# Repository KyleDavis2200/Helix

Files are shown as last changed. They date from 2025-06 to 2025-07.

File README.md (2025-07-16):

# Helix
Helix is an antweight ring spinner combat robot that uses its large weapon to protect itself from its opponents, instead of using normal armor.


# Features

* 10" asymmetric AR500 steel weapon spinning at over 260 MPH with 128 joules of energy!
* Vertical element to the weapon's counterweight blocks attacks from horizontal spinners before they hit the robot itself.
* Dual RS2205 Brushless Weapon Motors
* Tangent drive with tank treads.
* Carbon fiber frame
* Durable TPU body with ultra lightweight design.
* Custom PCB that serves as a switch, series board for the batteries, and a BEC for the receiver.

# Images
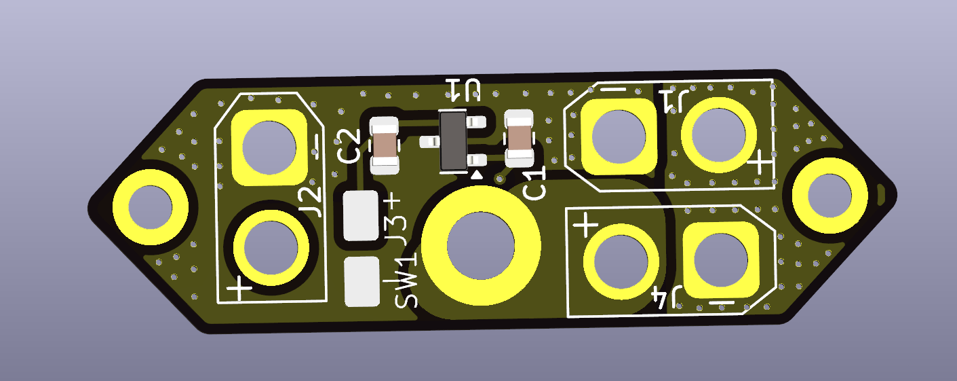
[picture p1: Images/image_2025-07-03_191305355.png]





# Background

Combat robotics has been one of my main hobbies ever since I joined my school's combat robotics team at the beginning fot he 2023-2024 school year. Throughout that time, I have mainly spent my time building 15lb eggbeater combat robots, where, due to the time and money invested into them, we are often scared to go too far outside of the box since a small design flaw could mean thousands of dollars and hundreds of hours were wasted. Highway is the perfect opportunity to make something outside of the box, as complex and creative projects are rewarded. 

# Bill of Materials

|Item |Individual Cost|Quantity |Total Cost (Includes shipping)|Notes |
|---|---|---|---|---|
|Drive Motor Screw |8.75 |1 (pack of 25)|8.75 |*Only 8 in the robot |
|Drive Standoff/WM Screw |6.4 |30 |6.4 |*Ordering extra screws in case some get lost or damaged. 24 are used in the robot. |
|Main Screw |4.36 |12 |4.36 |*Ordering extra screws in case some get lost or damaged. 8 are used in the robot. |
|M3 Plastite |5.69 |1(Pack of 25) |5.69 |*Only 6 in the robot |
|4in1 ESC |38.8 |1 |38.8 | |
|PCB |9.62 |1 |9.62 | |
|Battery |9.25 |2 |18.5 |*Need 2 because the robot uses 2 at once |
|Carbon Fiber Parts |29.1 |1 |29.1 | |
|Weapon |18.47 |2 |36.94 |*Only 1 is used in the robot, other is a spare |
|Bearing Washer |0.77 |5 |3.85 |*4 are used in the robot, 5th is a spare |
|Weapon Bearing |12.99 |1 (Pack of 10)|12.99 |*4 are used in the robot |
|Standoff |3.06 |1 (Pack of 5) |3.06 |*4 are used in the robot |
|Drive Standoff |8.99 |1 (Pack of 10)|8.99 |*8 are used in the robot |
|Repeat Tangent Drive Motor |22.5 |2 |45 |*2 are used in the robot |
|RS2205 Weapon Motor |7.6 |2 |15.2 |*2 are used in the robot |
|XR2 Receiver |9.99 |1 |9.99 | |
|Digikey |18.54 |1 |18.54 |*1x AP7381-50SA-7, 1x 2.2 uF 0805 Ceramic Cap, 1x 1 uF 0805 Ceramic Cap, 3x XT30 used on PCB, bought some extras because I'm new to soldering and am scared to mess it up|
| | | | | |
|8x M3 Washer |N/A |N/A |N/A |*Already Have |
|M5 x 12mm Screw |N/A |N/A |N/A |*Already Have |
|2x M5 Nut |N/A |N/A |N/A |*Already Have |
|M5 Washer |N/A |N/A |N/A |*Already Have |
|M3 Screw for Switch |N/A |N/A |N/A |*Already Have |
|M3 Nut for Switch |N/A |N/A |N/A |*Already Have |
|2x M2 Screws for PCB Mounting|N/A |N/A |N/A |*Already Have |
|2x M2 Screws for PCB Mounting|N/A |N/A |N/A |*Already Have |
|PLA Filament |N/A |N/A |N/A |*Already Have |
|TPU Filament |N/A |N/A |N/A |*Already Have |
|Nylon Filament |N/A |N/A |N/A |*Already Have |
| | | | | |
|Battery Charger |N/A |N/A |N/A |*Planning to buy myself |
|Transmitter |N/A |N/A |N/A |*Planning to buy myself because I want something a little nicer than what would be fair to buy from Hack Club's money |
| | | | | |
|Testing Cage |N/A |N/A |N/A |*Have access to one through my school's combat robotics team |
| | | | | |
| | | | | |
|Total |N/A |N/A |275.78 | |

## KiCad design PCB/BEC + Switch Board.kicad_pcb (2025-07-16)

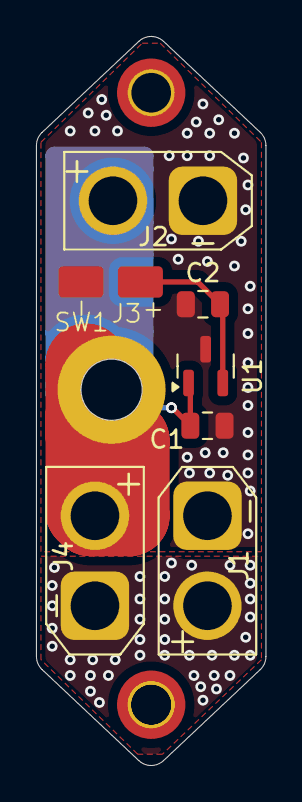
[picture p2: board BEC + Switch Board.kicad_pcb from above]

Board: 2 copper layers, 12.8 x 40.5 mm, 8 parts (1 on the bottom side), 4 nets.

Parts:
C1: 1uF; C_0805_2012Metric
C2: 2.2uF; C_0805_2012Metric
J1, J2, J4: Conn_01x02_Socket; AMASS_XT30U-M_1x02_P5.0mm_Vertical
J3: Conn_01x02_Socket; SignalWirePads
SW1: SW_DIP_x01; Screw Switch
U1: AP7381-50SA-7; SOT-23

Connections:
/GND: C1.1, C2.1, J1.2, J2.2, J3.2, U1.3 (GND)
unnamed: J1.1, J4.2
unnamed: C1.2, J2.1, U1.1 (VI)
unnamed: C2.2, J3.1, U1.2 (VO)

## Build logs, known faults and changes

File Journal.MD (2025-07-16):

---
title: Helix
author: Kyle Davis
description: A ring spinner antweight combat robot with a custom PCB for power distribution.
created_at: 2025-06-13
---

Total Time 28.75 Hours

6/13/2025

4 Hours

I began this project by searching for excuses to make an overly complicated combat robot. Combat robotics is my main hobby, but I have never ventured far outside of the meta out of fear of wasting time and money on an unsucessful bot. Hack Club's Highway program rewards projects that are extra complex with a higher budget and more points in the program. I saw this as the perfect opportunity to make a more complicated robot design. My previous experience in combat robotics comes from my 15lb robot, Dino, which I have placed 2nd and 3rd with at NRL Nationals over the last 2 years. Dino uses an eggbeater style weapon, which is very common and relatively simple. For this project I am going to use a more complicated weapon system, and maybe even a custom PCB, to make my project more complicated to warrant the higher budget and more points in Highway. This is something I have always wanted to do as well, as these more mechanically complex robots are always very fascinating, but Highway gave me the perfect justification to pull the trigger on it.

My first idea was to make a hammersaw, which uses a spinning weapon on an arm to attack the tops of other robots. However, the hammersaw has been very popular over the last year or two, especially in insectweights. This has led to the systems/parts needed to run a hammersaw being relatively well documented. I opted not to build a hammersaw as the well documented and convergant nature of hammersaw electronics/mechanics may cause me to not get the full points for Highway, which I would need to fund the build.

This led me to think about the most complicated robot designs I could think of, to make sure I could earn the full points and budget from Highway. My mind instantly went to ring spinners, which are typically very complicated due to the difficulty of constraining and powering such a thin blade. The advantage of this, however, is that you can build a robot where the blade sticks far enough out from your robot where you are able to reach your opponent while they have nowhere to target on your robot. I've always loved the idea of having a ring spinner, but I never quite fell in love with the idea of designing one, mostly due to the mechanical complexity. However, since I need complexity for this project, this is perfect as I am more comfortable adding mechanical complexity than electrical complexity.

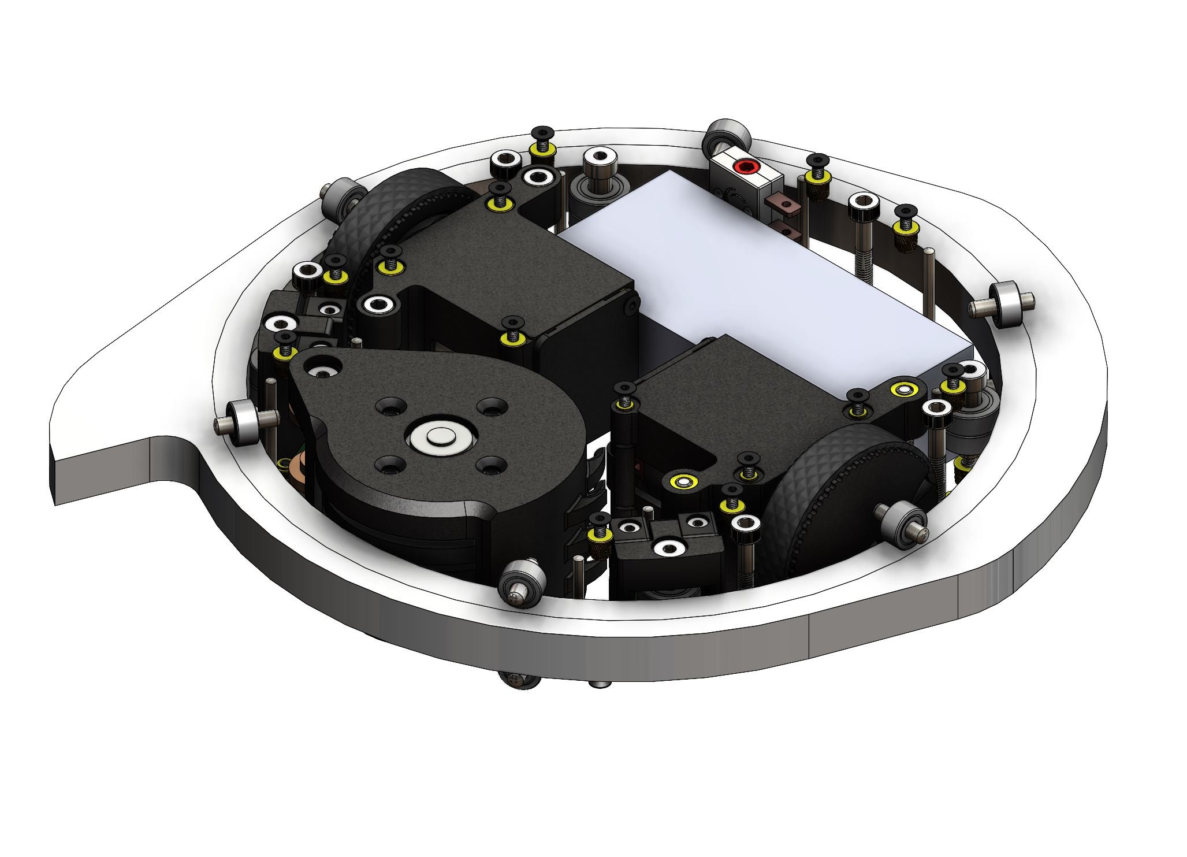
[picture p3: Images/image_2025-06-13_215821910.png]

An example of a ring spinner robot.

The first thing I did was design a rough blade concept. Some aspects of this design, such as the blade thickness, were based off of other antweight robots, such as the scalar kit. The amount of support everywhere around the blade was approximated by eyeballing it. I may attempt to use FEA in the future, but generally eyeballing works well enough in combat robotics(its also very difficult to approximate combat robotics collisions with FEA), especially after being in the community long enough to "calibrate" your eyeballing. This concept allowed me to check the mass of the blade, which I could then use to make sure that it would be possible to fit the robot in the weight limit. At 159 grams, the blade was very heavy, but its reach meant that I could get away with budgeting less weight for armor, giving me confidence that it would be possible to fit it within the weight limit.

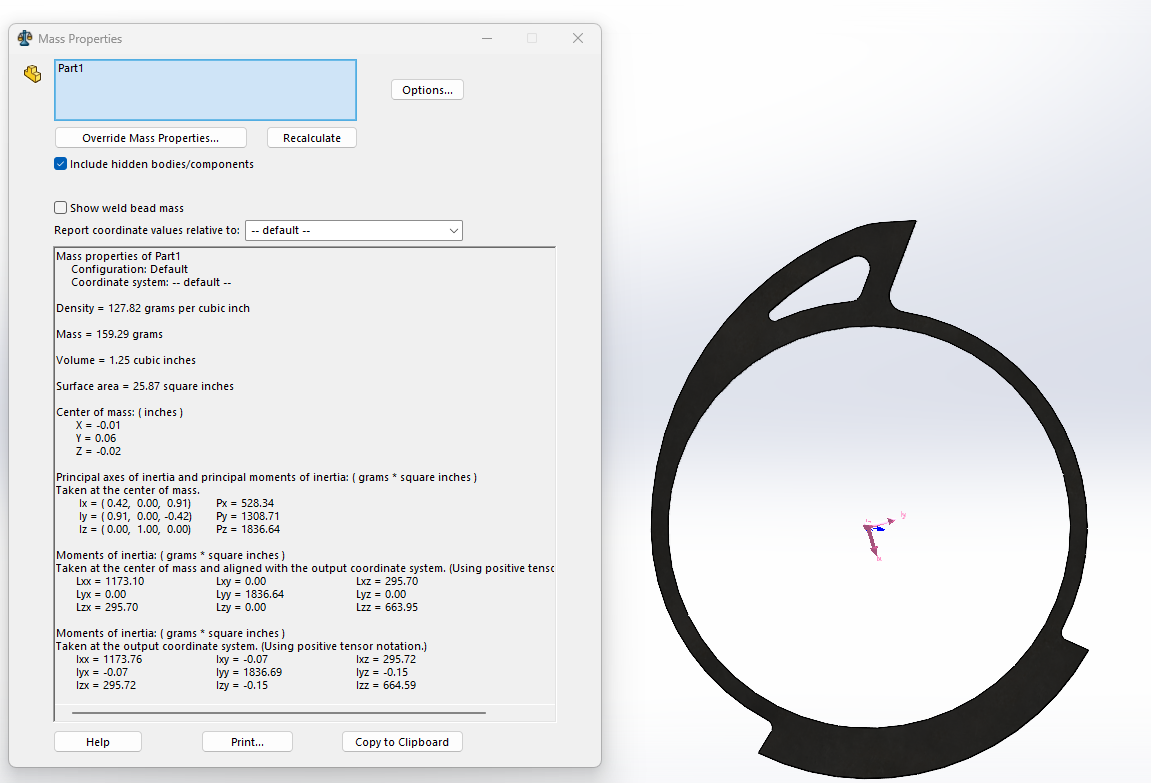
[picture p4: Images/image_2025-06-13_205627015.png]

The first blade design.

This design also allowed me to get a rough interior diameter of six inches, which I can then use to begin laying out the rest of the robot's design. Ideally, I would decrease this diameter, but I first had to make sure I could fit my electronics in it. The next step is to find the bearings I am going to use. This will allow me to get an idea of how much space I have for the electronics, as everything else can move more freely than the bearings. My initial plan was to have bearings above and below the blade, which would have constrained it axially. I did not consider that this would provide no radial constrainment, leading to the need for even more bearings. This system would have needed at least 9 bearings, and at 4g per bearing this would not be optimal with already being tight on weight from the large weapon. Instead, I am going to opt to use flanged ball bearings, where I can get away with using only 6 or less bearings at a relatively similar weight to the ball bearings above. This approach has its own flaw however. The flange on the bearings is so small that it may not provide enough axial constrainment by itself. To supplement them, I am going to use washers between the flange and the weapon ring. Since the washer goes all the way around the bearing, it has much more surface area constraining it, and the higher diameter of the washer allows it to provide more surface area for the weapon. At this point I realized I am likely going to greatly exceed the speed ratings on these bearings, which is normal for combat robots as they are only used for very short periods of time, however not to this extent as I may exceed 100k rpm on these bearings. There's not really anything I can do about that though so it is what it is.

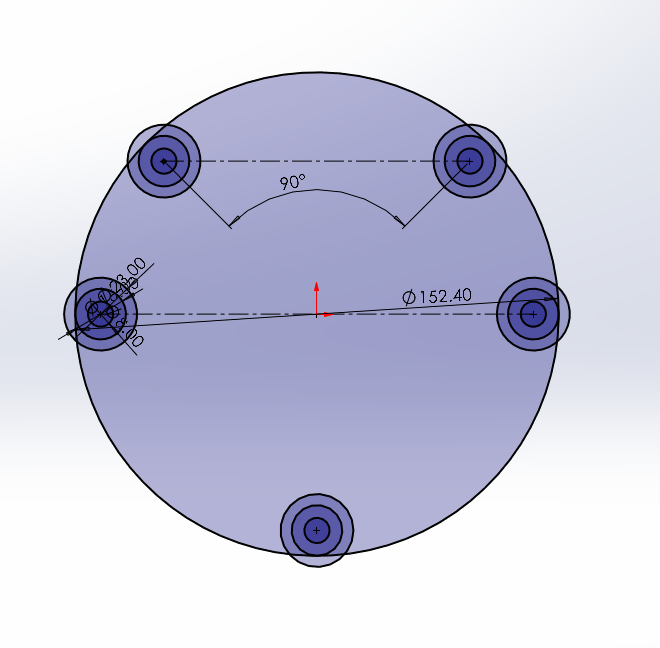
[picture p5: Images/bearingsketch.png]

Current sketch of the internals of the robot.

The next step was to choose my drive system. To keep everything on the robot simple I am going to use a tangent drive system. This eliminates the need for gearboxes or gear reduction as the motor output shaft uses friction to drive the wheels. Repeat Robotics sells motors designed specifically for this usage in this weight class, so I will use those. I plan on coupling this with Lego wheels, as that seems to be a very standard pairing. However, if the diameter of these wheels ends up being significantly larger than the height of the rest of the robot, I may opt for smaller custom wheels instead. At this point I also modeled in a 4S 300mah LiPo battery and a Repeat 2822 weapon motor that would friction drive the ring through a TPU interface.

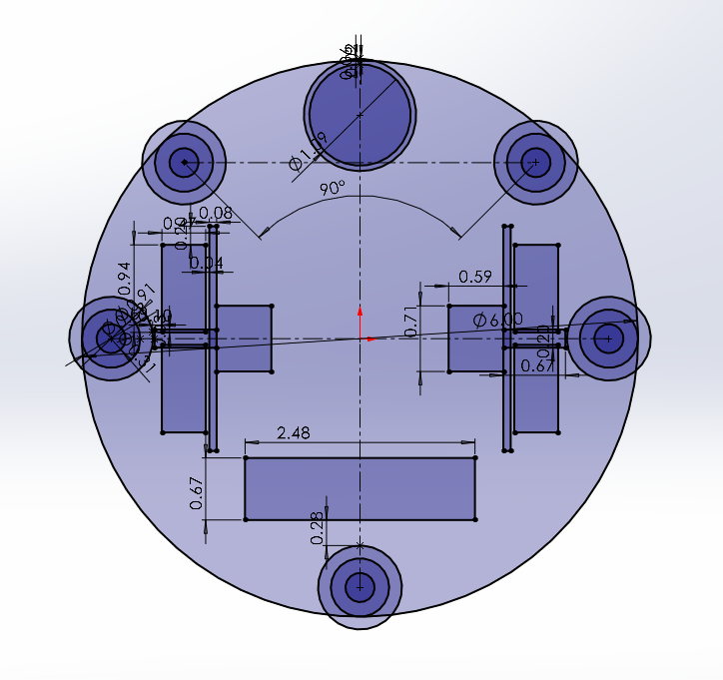
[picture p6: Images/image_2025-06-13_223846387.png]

Current design progress.

Clearly, I had way too much room on the inside at this point, so I chose to shrink it until I knew I could just barely squeeze the wiring in. This was important as the weight was approaching 324 grams, leaving approximately 120 grams left for the entire frame, receiver, wheels, receiver, and ESCs, but by shrinking the space I gave myself on the inside, I can shrink the weapon too, saving more weight.


Current weight.

By shrinking the internal ring diameter down to 5.25", I was able to knock a significant amount of weight out of the weapon, and this would also reduce the amount of weight spent in the remainder of the frame as the frame too would now be smaller. 

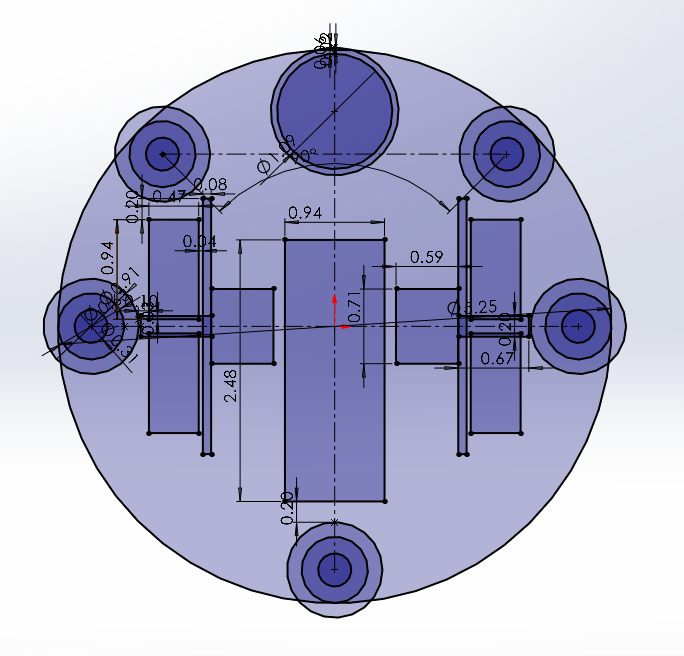
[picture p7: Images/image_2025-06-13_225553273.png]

Current internal layout.

I plan to proceed with this layout tomorrow as I model the frame, however I expect to encounter weight issues very shortly into my design process. My plan to save weight from there is to remove the rear bearing and reposition the remaining four bearings in a more square shape, allowing the battery to move further back and get rotated to fill up the created space. This would then allow me to shrink the robot more. This would save plenty of weight between the reduction in frame size, weapon size, and bearing count. I initially wanted to have five bearings as it would allow me to have three bearings supporting against the axial forces of upwards impacts and two against the axial forces of downwards(or, more likely, upwards impacts while inverted) impacts, however two of each would likely be plenty.

6/14/2025

6 Hours

Well, after thinking about it some more, I realized I should just got to the four bearing setup. This would save some weight and allow me to compact the robot more, which is always ideal. I would like to use extra weight for armor or for a fork on the back of the robot(unconventional for a ring spinner but counters the counter to the weapon). I also realized that the Repeat 2822 weapon motor that I planned on using would have been too big, sticking out past the top plate, and would have caused the robot to not be invertible. Instead, I replaced it with two 2205 drone motors, which should provide more than enough power. A single one of these motors could probably spin up the weapon, just barely, but due to the size of the weapon more motor is ideal. 

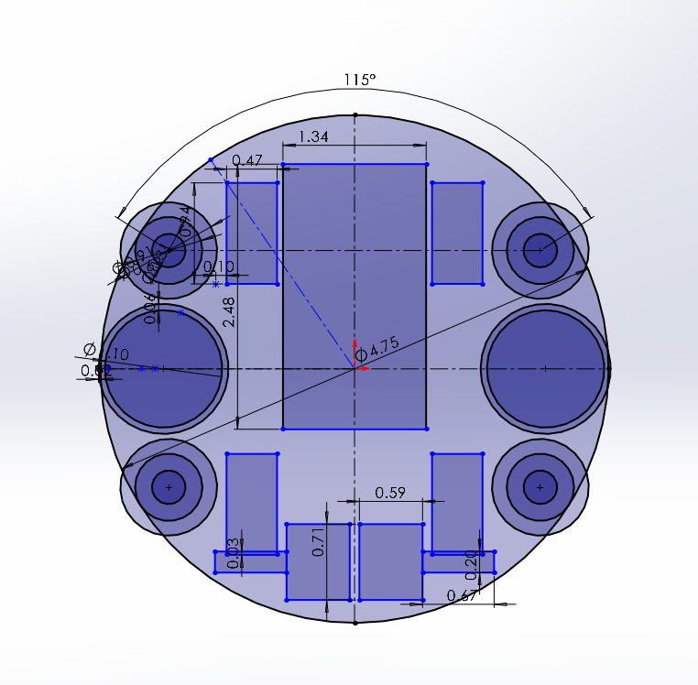
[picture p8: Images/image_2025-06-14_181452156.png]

This was the setup that I arrived at.

I still felt like there was a bit more space to be squeezed out. One of the flaws with this setup is I needed to find space for belts to power the front wheels, and I didn't leave much space for this. My next step was to look into using tracks instead of wheels, as these would allow me to save more internal space as I can use two small pulleys for each the front and back of the tracks, creating a more rectangular profile, saving space on the inside of the robot. I initially looked into silicone timing belts and silicone coated timing belts, but I would have need to custom order them. Next, I looked into using silicone wrist bands, but they would have been slightly too short. Instead, I opted to use round belts which I could make to the exact length that I needed by melting them together at the right length.

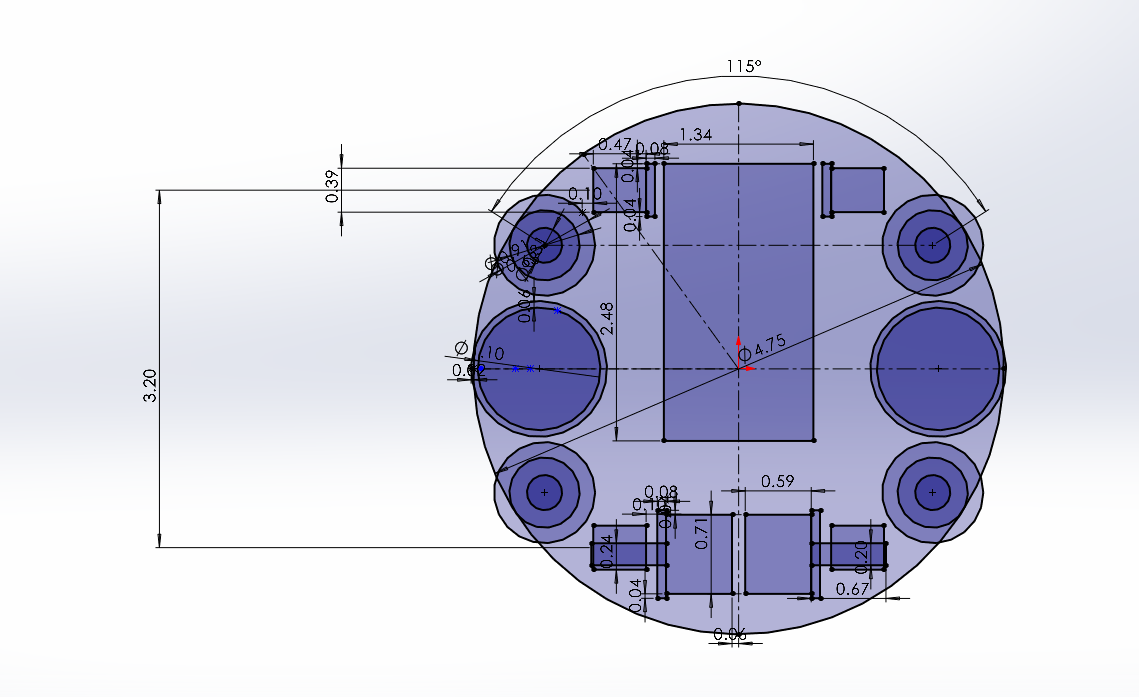
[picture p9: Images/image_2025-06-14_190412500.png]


This layout, with the space gained from the treads, was much more comfortable. Each track/belt weighed approximately 2 grams, which seemed bearable. Next, I made a sketch of the side of the robot, which would guide my extrusion thicknesses in the next step.

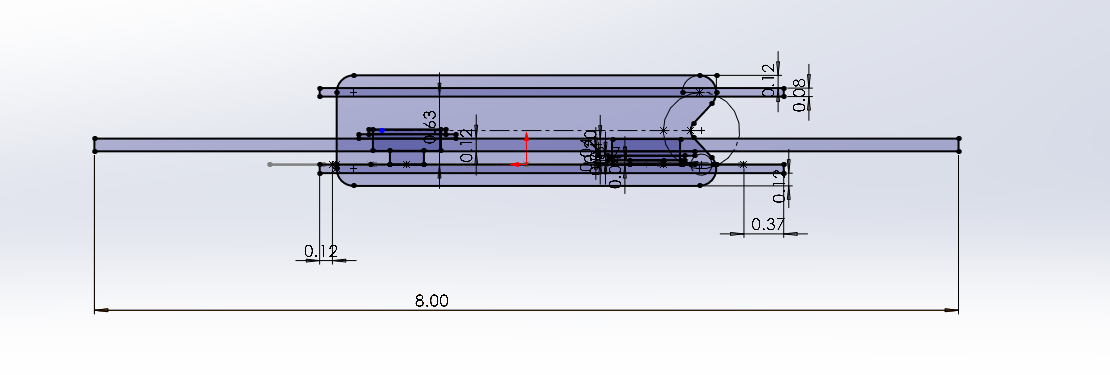
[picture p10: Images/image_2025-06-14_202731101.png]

Oops! All weapon (: !

Next, I extruded everything according to the sketches I made above. This outlines the construction of most of the robot's structure and its weapon system structure pretty well. The top and bottom of the robot are made of 2mm carbon fiber and provide most of the strength. There are 8mm aluminum standoffs in the four corners to hold the weapon bearings. Underneath and above each bearing are PLA spacers to get them at the right height. The bearings have aluminum washers on them to increase the surface area of the flanges in contact with the weapon, aiding in the axial constrainment. Two of the bearings have their flanges and washers under the weapon, and two of them have them above the weapon, to provide support in both directions. The next step is to implement the mounting for the drive pulleys and motors.

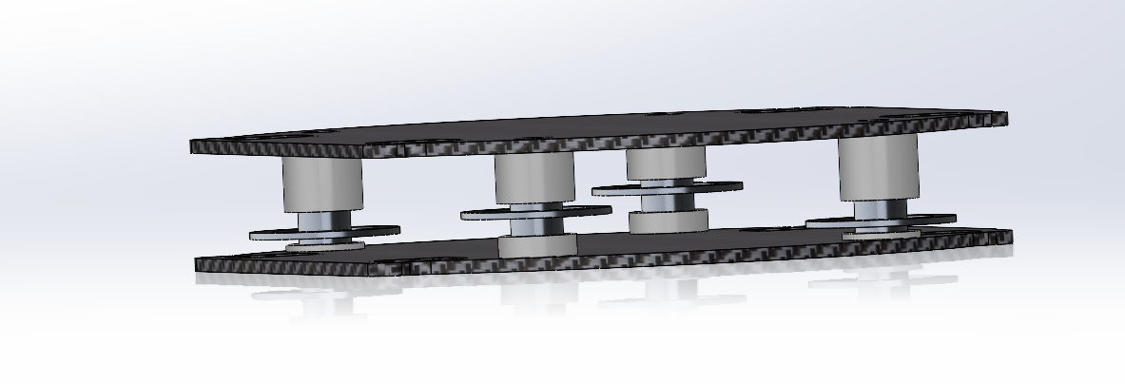
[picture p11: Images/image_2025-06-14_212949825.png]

Current design.

Instead of doing the productive next step I described above, I created an assembly file(I do my frame as a multibody part) and inserted the weapon.

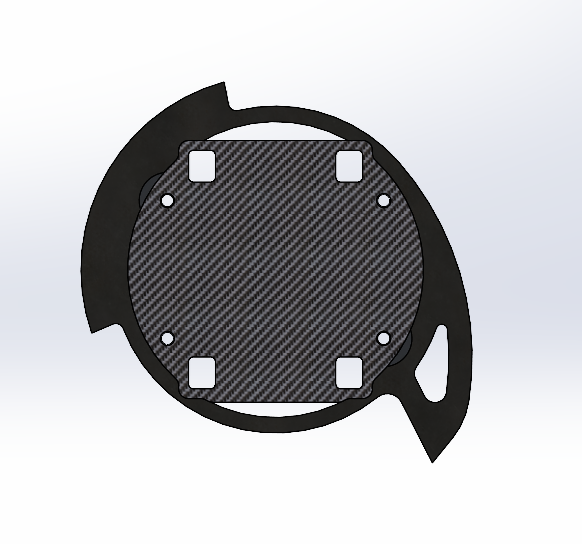
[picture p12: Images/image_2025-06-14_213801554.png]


Yeah this thing is ridiculous.

At this point I realized that the robot would be impossible to assemble due to the drive tracks needing to go through the top and bottom plates. I changed this by making cutouts in the top and bottom plate where they could be slid in between the treads. This also saved weight and removed a fragile area that was likely to result in the plates cracking. At this point I also realized I had to create cutouts in the top plate around the weapon (not pictured) motor since there was still 0.7mm of interference even after switching to a smaller motor. I may find a way to undo this or create a cover for it later, but for right now this is what I had to do.

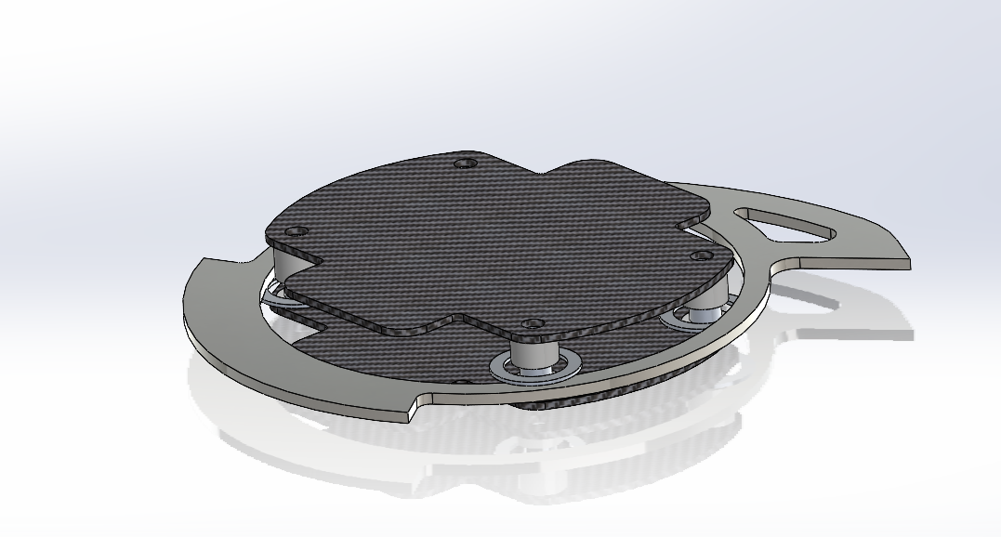
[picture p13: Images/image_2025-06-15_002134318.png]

Current design progress.

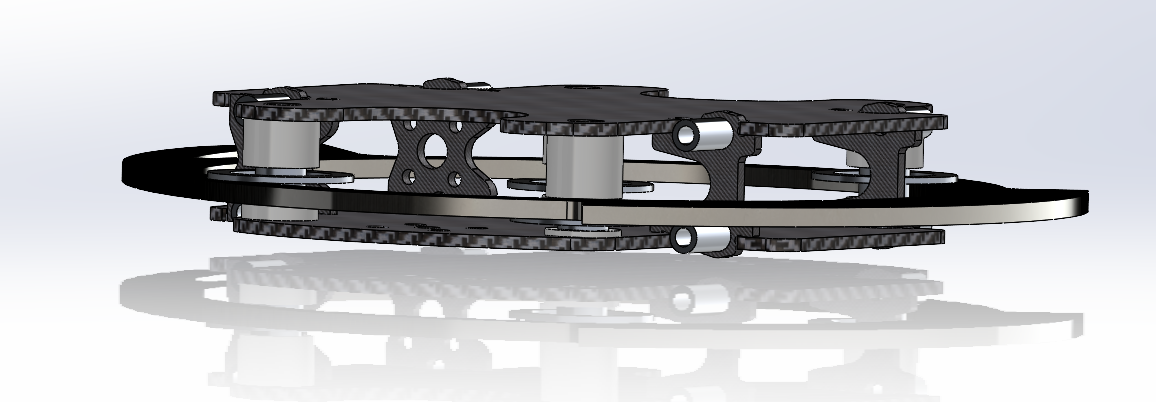
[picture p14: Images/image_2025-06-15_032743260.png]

At this point, I added all the features for mounting the drive motors and the drive pulleys. The mounting plates use dogbones to key into the top and bottom plates, allowing them to have a healthy amount of strength without using any fasteners yet. I will likely add a single screw to each plate later once I am adding the TPU armor.

At this point, I have about 100 grams left for ESCs, a series board for the batteries, a receiver, and any armor. Since each of those items besides the armor is just a couple grams I am not too worried about weight, but the armor weight can add up quickly. However, the whole idea behind this design was to "hide" behind the large weapon, so I am probably going to use very minimal armor.

6/15/2025

3 Hours

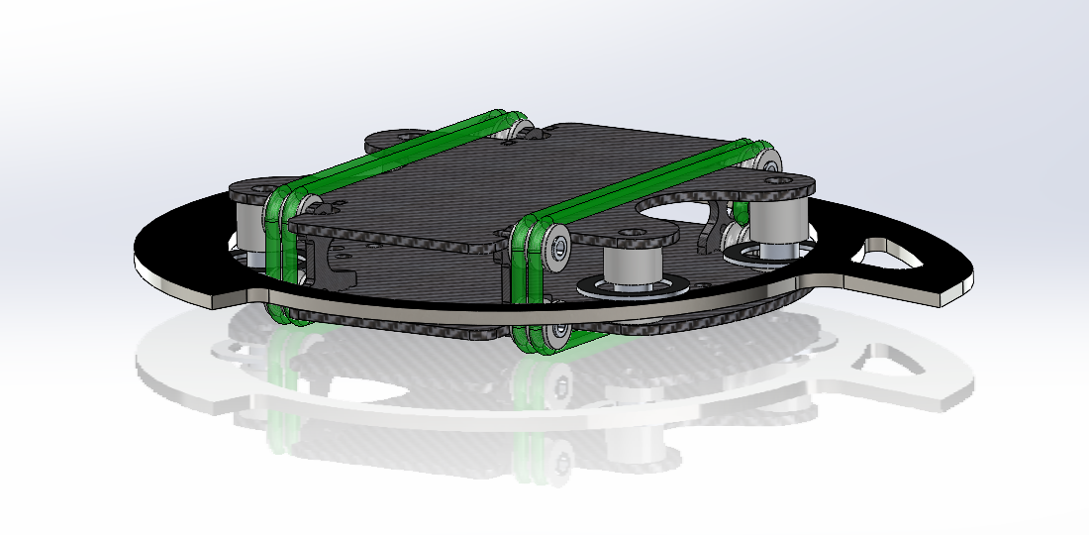
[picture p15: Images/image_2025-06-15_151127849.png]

At this point, I modeled in the drive pulleys and the belts/tracks. 

Now, I decided to add in the rest of the components into the model so that when I design the armor/body I know what I have to protect.
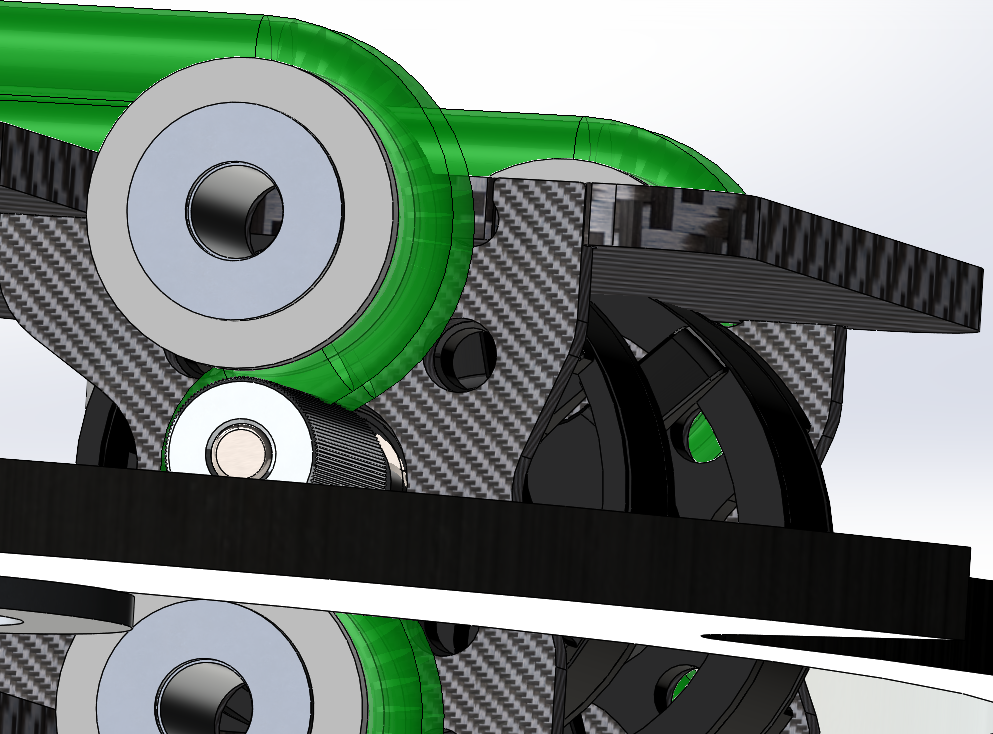
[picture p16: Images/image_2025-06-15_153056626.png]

Adding in the drive motors revealed a couple flaws. I messed up when calculating the interference for the drive belts, so the motors need to get moved to the back more or the pulleys need to move forwards (with the belts being made shorter accordingly). I also forgot to add the pockets for motor clearance in the top and bottom plates.

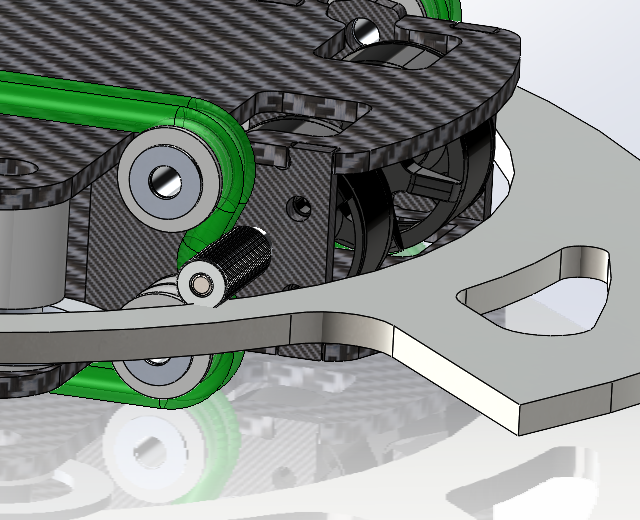
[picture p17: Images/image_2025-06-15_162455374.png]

At this point, I got the drive motors to pretty much fit, but I will need to trim the shafts. The other issue is that two of the motor mounting screws interfere with the wheel pulleys and standoffs, so I may need to use countersunk screws in carbon fiber, which is suboptimal but I don't have many other choices.

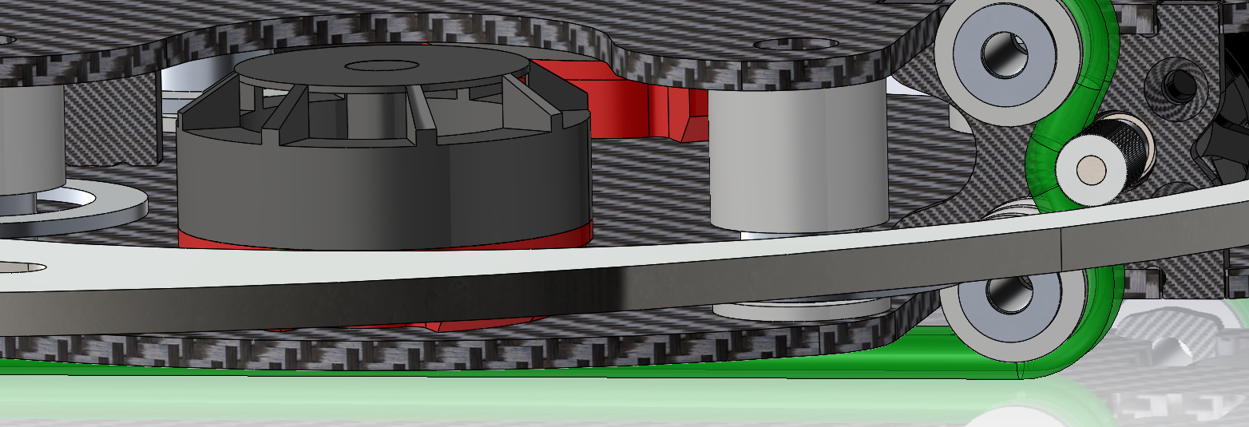
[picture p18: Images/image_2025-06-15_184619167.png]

Now, I countersunk the drive motor mounting screws, inserted the weapon motors, and cut down the shafts on both the drive motors and the weapon motors. The issue I am facing now is that the weapon motor has a red part where it mounts which does not spin, and that happens to line up perfectly at the height of the blade. Making my blade as low as possible is ideal against vertical spinners, so I wanted to keep the blade low, and mounting the motors to the top would make assembly more difficult, so instead I will solve this by thickening up the plastic(nylon or TPU, not sure yet) interface layer between the motor and the ring to be stiff enough where it can drive the ring without being directly supported by the motor can.

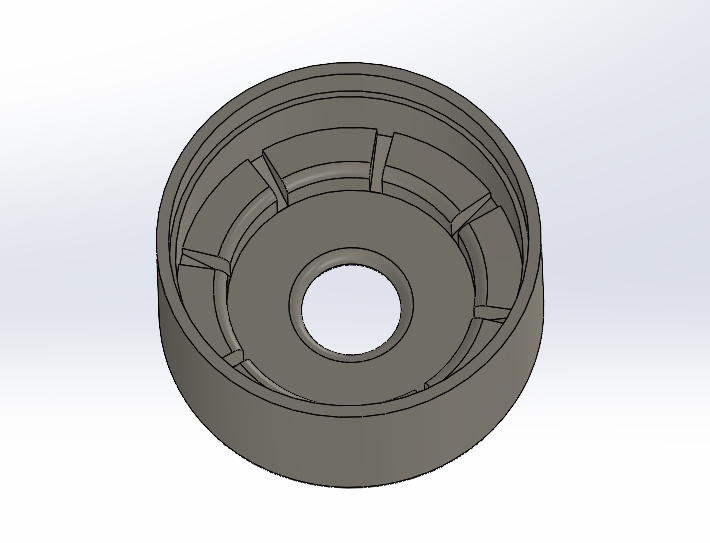
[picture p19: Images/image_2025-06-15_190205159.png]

The interface layer is a pretty simple part. Its basically just a cylinder with a keying feature for the top of the motor and a slight step to provide clearance for the part of the motor that does not spin. I will probably be gluing or taping this onto the motor as there is not a way to screw anything onto this motor with the shaft cut off and axial forces are not a concern.

6/25/2025

0.25 Hours

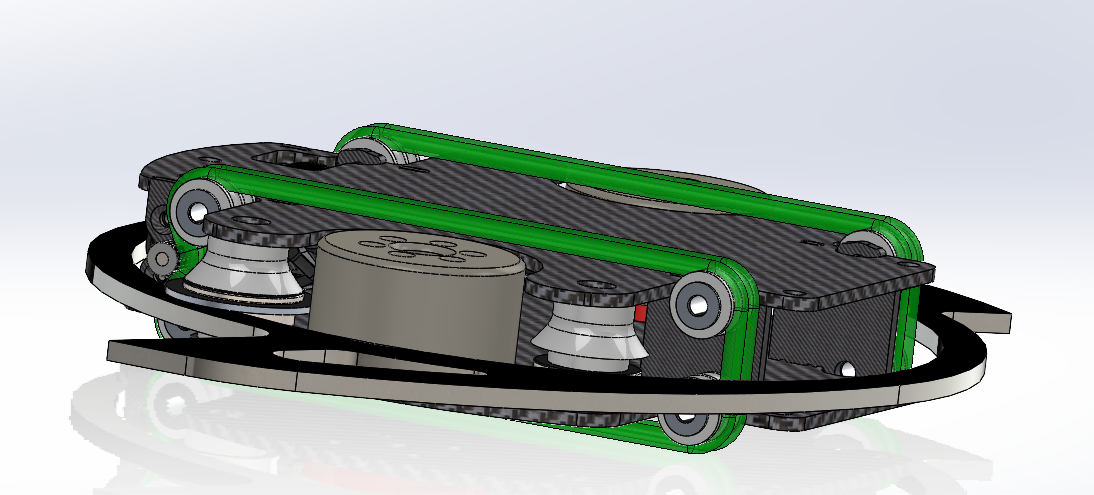
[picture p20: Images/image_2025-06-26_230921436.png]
 
Just barely worked on it today. Flared out a portion near the bottom of the upper spacers on each standoff to provide vertical support for the TPU body that will rest on it.

6/26/2025

4 Hours

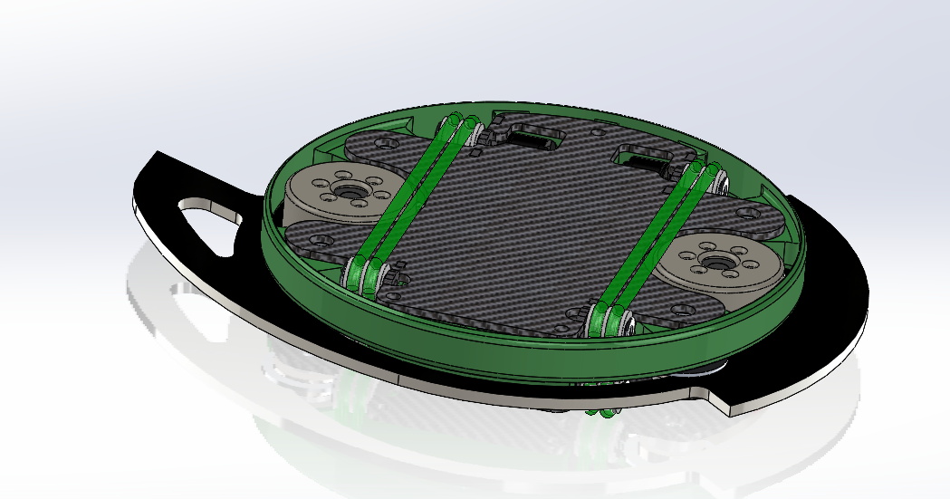
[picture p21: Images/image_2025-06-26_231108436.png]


Today I modeled a super minimal TPU body/armor for the robot that protects from attacks and serves to keep the electronics in. Since the whole concept of this robot revolves (haha) around the weapon serving as the first line of defense, this armor system was super minimal, generally consisting of 2-4 walls 0.4mm thick walls with low infil. Even if the weapon goes down, it still has a steel ring around the entire robot that will serve as armor. The TPU armor ring is generally spaced out from most of the robot's critical components, so if an opponent manages to hit it and tear through it, they'll be unable to hit anything that would cause significant damage.

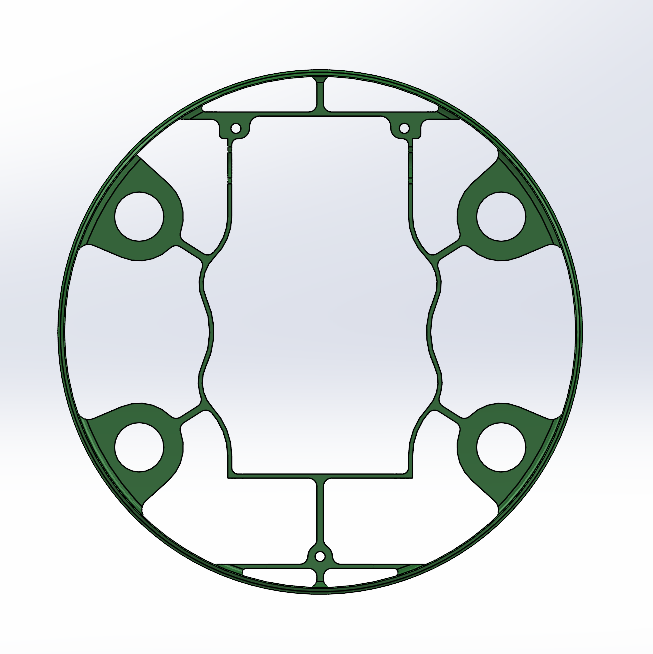
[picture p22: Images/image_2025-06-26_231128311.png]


On the inside of the robot, the armor has another layer that holds all of the electronics within the frame. This keeps everything in place and prevents wires from getting tangled in the motors.

7/1/2025

2 Hours

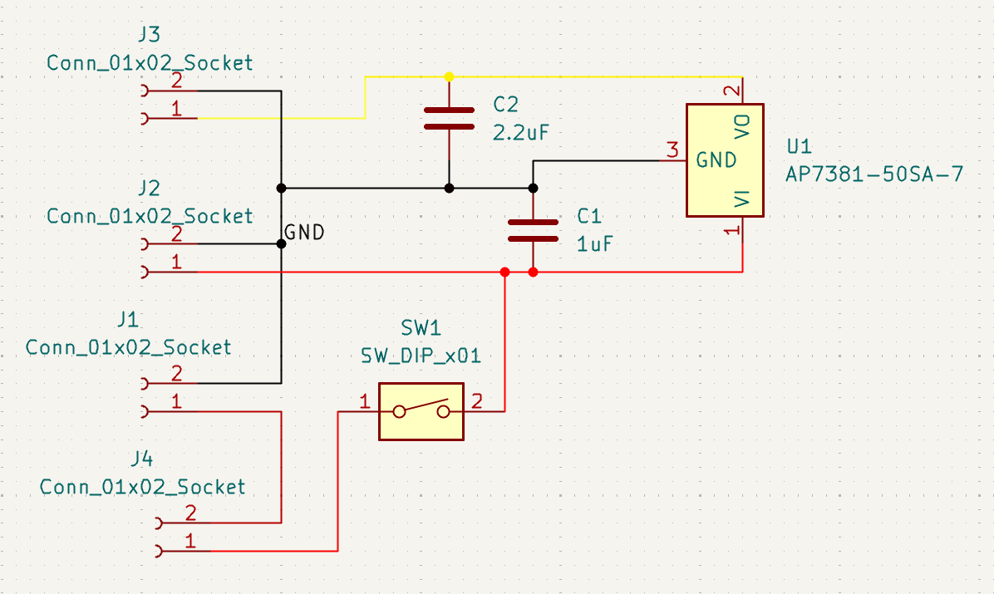
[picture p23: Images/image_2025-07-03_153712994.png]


Created a schematic for a basic PD Board / Switch / BEC for the robot. This was inspired by the Just Cuz Robotics PD Boards.

7/2/2025

4 Hours

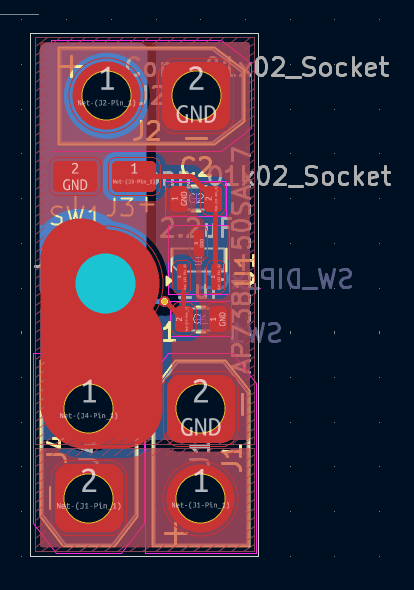
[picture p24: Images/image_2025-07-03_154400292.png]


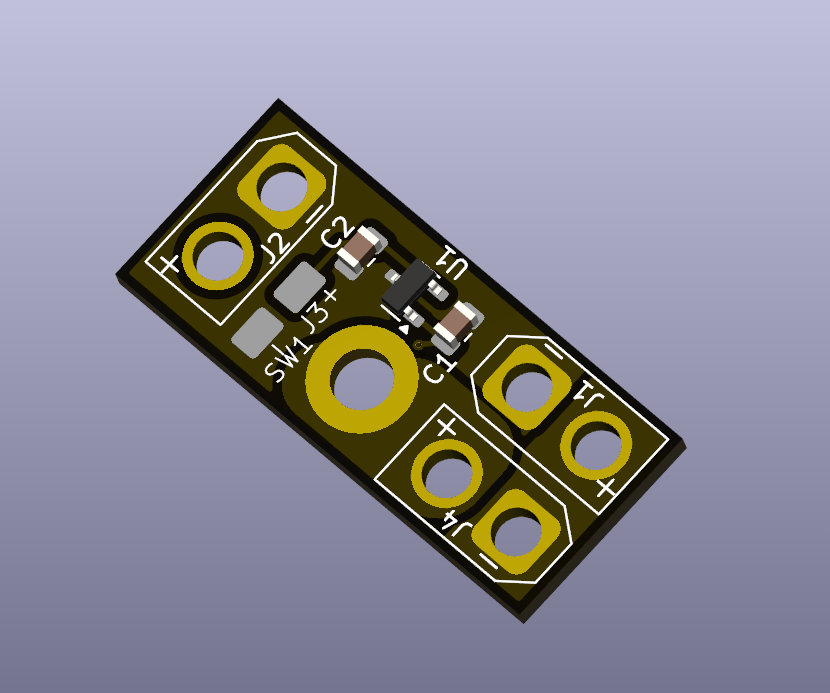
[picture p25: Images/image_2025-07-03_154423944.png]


Created a layout for the PCB. The board has two XT30 connectors to connect to each battery (batteries are in series), and a third to output power to the rest of the 4in1 ESC. The switch is an M3 screw with a nut soldered onto the board. There is a linear regulator that serves to create a 5V output for powering the receiver.

7/3/2025

3 Hours

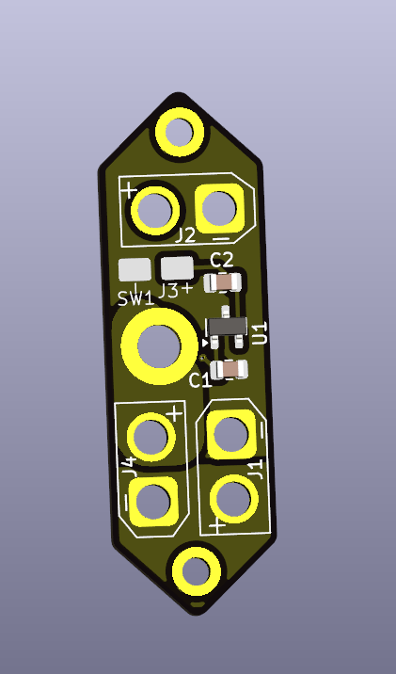
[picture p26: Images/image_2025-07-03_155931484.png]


Created mounting holes for the PCB. This will allow me to lock it in one place so the switch is always accessible, which is important for safety reasons. Last thing I have to do for this PCB is via stitching.



With via stitching done, the PCB is finalized and I can work on making a finalized BOM after I get a quote from JLCPCB.

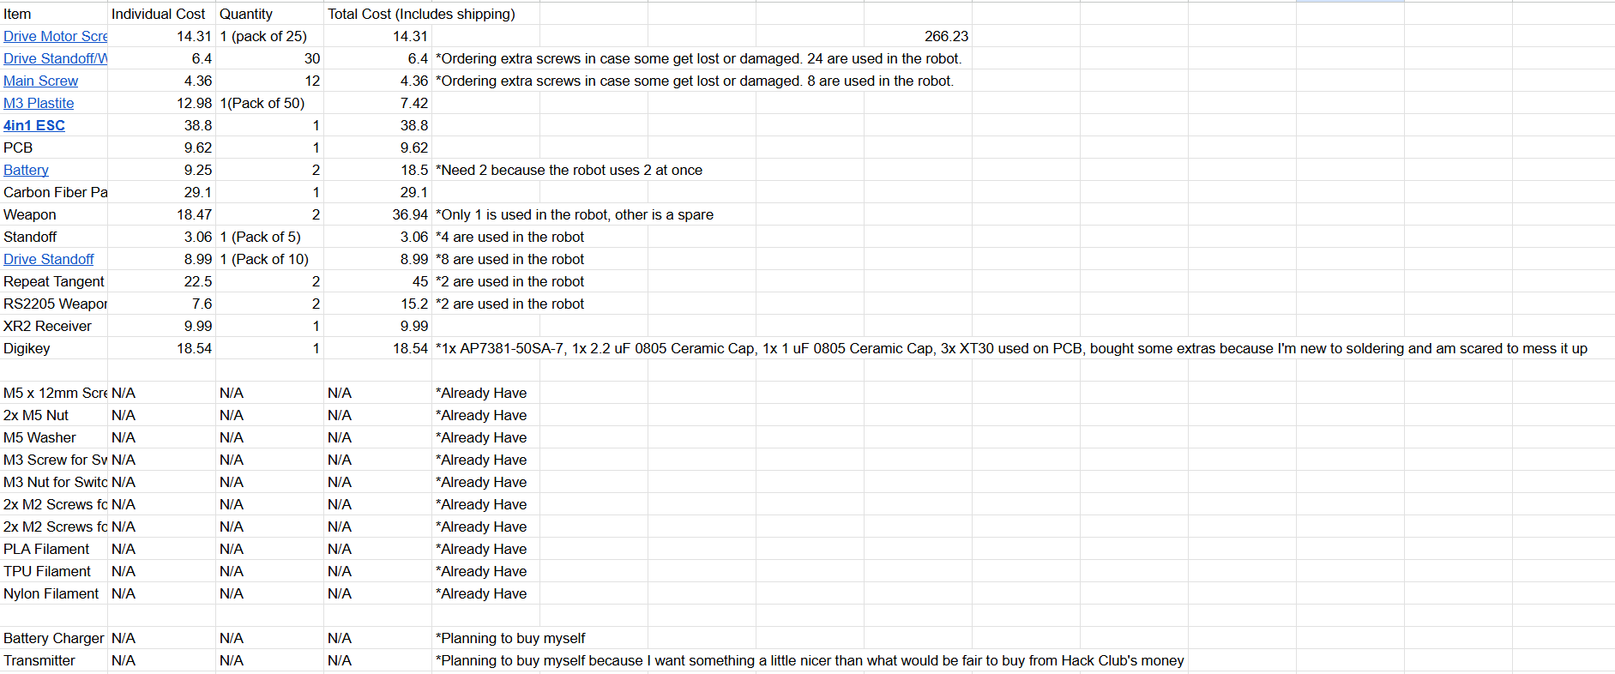
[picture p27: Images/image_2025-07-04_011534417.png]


I got my BOM put together. Everything came out a little bit more expensive than I would have liked, but I'm still well under the $350 budget for 10 point projects, and I believe this project deserves 10 points due to the extra complexity from the ring spinner design and the custom PCB.

7/4/2025

1.5 Hours

Today I focused on updating the README and shipping my project. I also added in screws to the CAD model to put the finishing touches on its aesthetics. However, I ran into an issue:

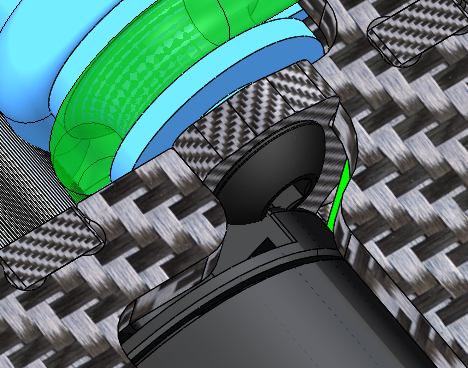
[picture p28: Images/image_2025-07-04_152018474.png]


My plan to fix this is going to be to space the motor away from the screws using washers or spacers, but that means extra weight and a further delay on finishing this project, meaning I am going to miss the opportunity to fight it at Undercity (which I was already far too late to have a chance at tbf), and at the SEMO event the week after. Designing in the spacers themselves is not a big delay, but needing to get quotes for new carbon fiber parts is a significant delay with the holiday weekend.

7/16/2025

1 Hour

Shipped the project!
